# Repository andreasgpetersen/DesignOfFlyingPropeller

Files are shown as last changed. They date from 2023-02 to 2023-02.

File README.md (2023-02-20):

# Design Of Flying Propeller
Bachelor thesis at DTU 2020. This thesis focuses on building, programming, and controlling a novel type of dronedesign. The drone behaves like a helicopter rotor as it rotates around its z-axis to cre-ate the lift necessary to keep it airborne.

Test flight while suspended mid air: https://www.youtube.com/watch?v=Mw67W8S0a4E

The drone has three large wings, and rotates around its own z-axis to create lift, with one Teensy Microcontroller to control each wing. 
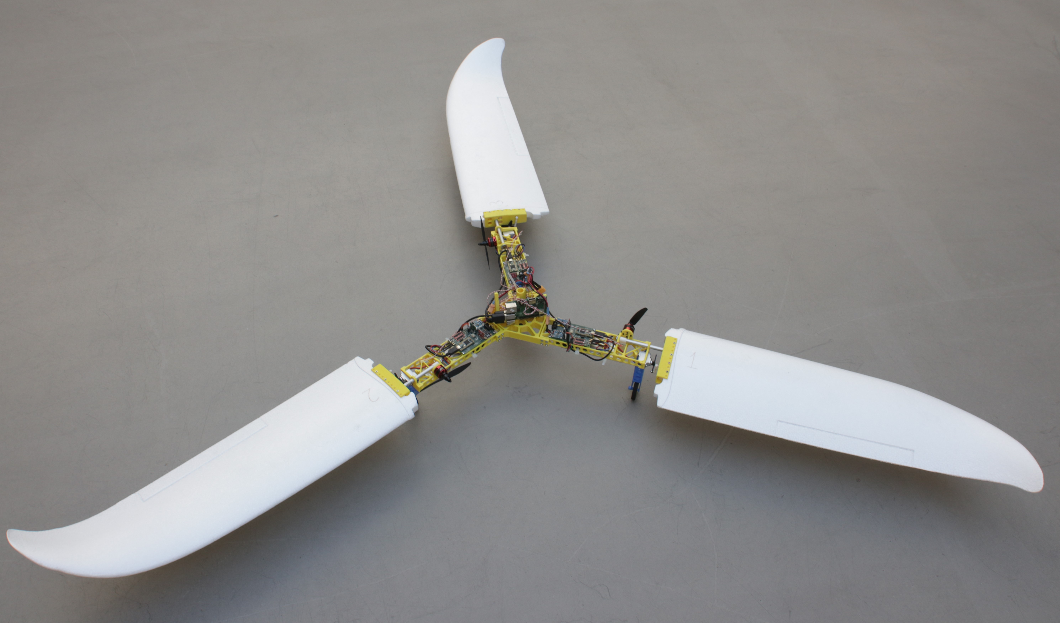
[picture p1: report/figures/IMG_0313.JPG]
Photo of final drone


All three Teensy boards send oirentation/location data to the Raspberry Pi which then computes the next control inputs. This runs in an infinite loop. The communication and power channels of the drones can be seen below: 
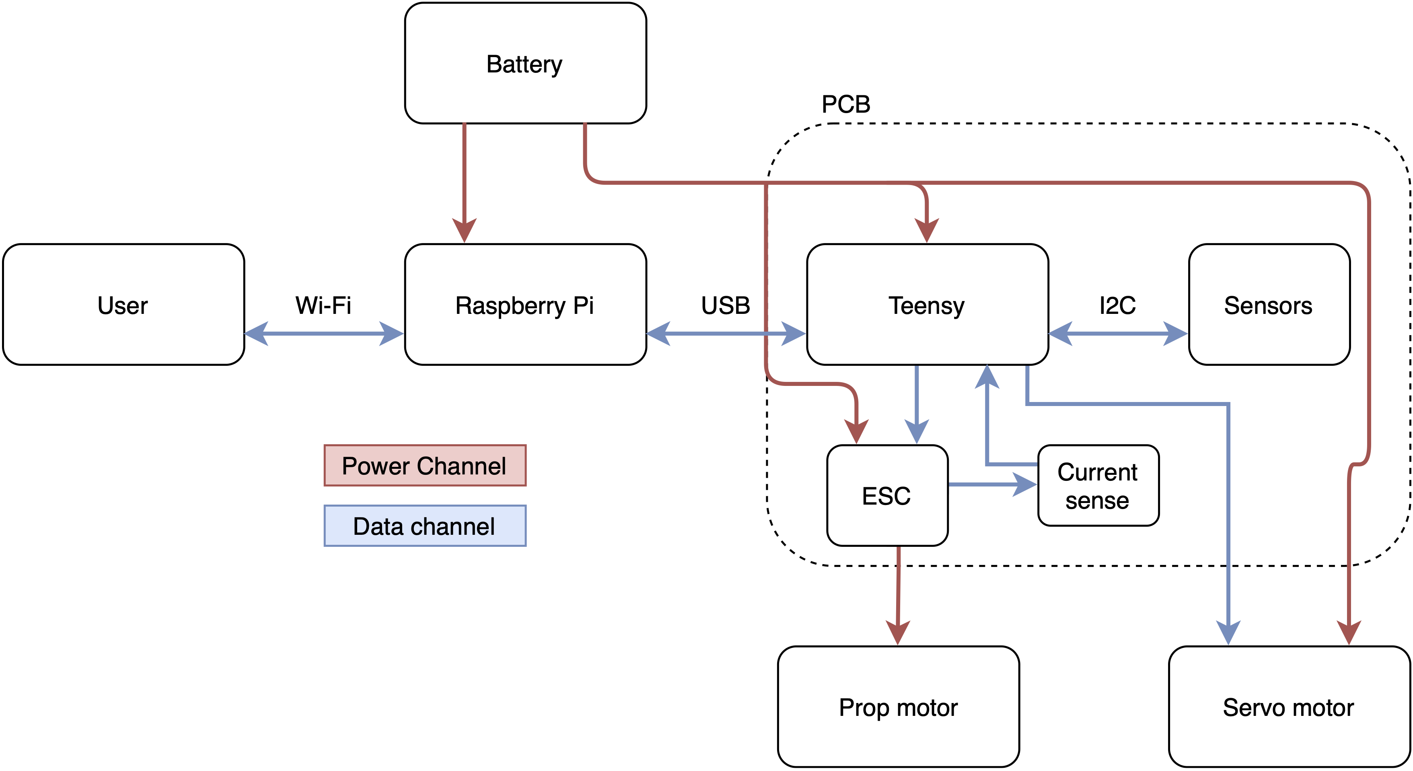
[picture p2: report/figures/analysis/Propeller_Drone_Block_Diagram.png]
Overview of communication and power channels


This code consists of two components:

1) communication_rpi2teensy, which is Python 3 code to be run on a Raspberry Pi (only tested for 3B+).
   The three Teensy board should be connected to the RPi using USB.
   In the folder you will find:

    A) communication_functions.py
    B) concurrent_control.py

	A) is a file that contains functions for communications for B) to execute
	B) is the main script which should be executed. Either it is configured for running a control loop
	with a set reference point, or it can be used as a menu for debugging functions. At all times
	the script logs data to a file which name is the days date and time. 
	
2) wing_ctrl_v2, which is C++ code that runs on a Teensy microcontroller (only tested for Teensy 3.2)
   In the folder you will find:
    A few example output log files
    B) .pio, which stems from PlatformIO. PlatformIO is used when programming the microcontrollers. It runs in 
    many IDEs and hackable text editors: https://docs.platformio.org/en/latest/integration/ide/vscode.html#installation
    C) .vscode which stems from Visual Studio code
    D) include, which is empty
    E) lib, which is empty but holds place for libraries
    F) src, which contains the code that runs on the microcontrollers
    G) test, which is empty
    H) platformio.ini which is used by PlatformIO extension
    
    F) is the only file that really matters, the rest is a byproduct of using PlatformIO. It runs a continous loop
    on the Teensy, in which it calculates orientation of the device and its sensor as well as issues commands
    to the propeller and servo motor

To use the code:
On the RPI, you download the scripts to a place of your choice, and run the scripts from the commandline
like you would with regular Python scripts, ie.: python3 concurrent_control.py 
Remember to install the approiate Python packages. The newest version of Python available on the RPi was used.
Consider using a virtual env to minimize errors with packages and versions. 

On the microcontroller, we used PlatformIO for programming. It runs well in Visual Studio Code.
To get started with PlatformIO follow the instructions here: https://docs.platformio.org/en/latest/integration/ide/vscode.html#installation
Remember to install Arduino IDE and Teensyduino: https://www.pjrc.com/teensy/td_download.html

When done, import wing_ctrl_v2 to PlatformIO and build the program. If you have trouble with libraries not being
found, remember to only build the code when you're in the wing_ctrl_v2 folder.
If it succeeds (which it does at the time of writing, June 25th 2020), upload it to each Teensyboard using
the inbuilt function in PlatformIO. Remember to change the boardnumber to the correct one to use the correct
calibration.

All boards are calibrated to be used in ASTA at DTU. If used elsewhere, recalibrate. 

This code has been developed by Jonas Brøndum (s173952@student.dtu.dk) and
Andreas Grønbech Petersen (andreasgp@protonmail.com / s173901@student.dtu.dk)
as part of a Bachelor Thesis in Electrical Engineering at DTU, June 2020

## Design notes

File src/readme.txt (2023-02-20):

Source code for Flying Propeller - A Bachelor Thesis 
This code consists of two components:

1) communication_rpi2teensy, which is Python 3 code to be run on a Raspberry Pi (only tested for 3B+).
    The three Teensy board should be connected to the RPi using USB.
    In the folder you will find:

    A) communication_functions.py
    B) concurrent_control.py

	A) is a file that contains functions for communications for B) to execute
	B) is the main script which should be executed. Either it is configured for running a control loop
	with a set reference point, or it can be used as a menu for debugging functions. At all times
	the script logs data to a file which name is the days date and time. 
	
2) wing_ctrl_v2, which is C++ code that runs on a Teensy microcontroller (only tested for Teensy 3.2)
    In the folder you will find:
    A few example output log files
    A) .pio, which stems from PlatformIO. PlatformIO is used when programming the microcontrollers. It runs in 
    many IDEs and hackable text editors: https://docs.platformio.org/en/latest/integration/ide/vscode.html#installation
    B) .vscode which stems from Visual Studio code
    C) include, which is empty
    D) lib, which is empty but holds place for libraries
    E) src, which contains the code that runs on the microcontrollers
    F) test, which is empty
    G) platformio.ini which is used by PlatformIO extension
    
    E) is the only file that really matters, the rest is a byproduct of using PlatformIO. It runs a continous loop
    on the Teensy, in which it calculates orientation of the device and its sensor as well as issues commands
    to the propeller and servo motor

To use the code:
On the RPI, you download the scripts to a place of your choice, and run the scripts from the commandline
like you would with regular Python scripts, ie.: python3 concurrent_control.py 
Remember to install the approiate Python packages. The newest version of Python available on the RPi was used.
Consider using a virtual env to minimize errors with packages and versions. 

On the microcontroller, we used PlatformIO for programming. It runs well in Visual Studio Code.
To get started with PlatformIO follow the instructions here: https://docs.platformio.org/en/latest/integration/ide/vscode.html#installation
Remember to install Arduino IDE and Teensyduino: https://www.pjrc.com/teensy/td_download.html

When done, import wing_ctrl_v2 to PlatformIO and build the program. If you have trouble with libraries not being
found, remember to only build the code when you're in the wing_ctrl_v2 folder.
If it succeeds (which it does at the time of writing, June 25th 2020), upload it to each Teensyboard using
the inbuilt function in PlatformIO. Remember to change the boardnumber to the correct one to use the correct
calibration.

All boards are calibrated to be used in ASTA at DTU. If used elsewhere, recalibrate. 

This code has been developed by Jonas Brøndum (s173952@student.dtu.dk) and
Andreas Grønbech Petersen (s173901@student.dtu.dk)
as part of a Bachelor Thesis in Electrical Engineering at DTU, June 2020

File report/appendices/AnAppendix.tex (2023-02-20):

%!TEX root = ../Thesis.tex
\chapter{Extra system graphics}
\begin{figure}[h]
    \centering
    
    \caption{Closed loop frequency response (from $\omega_{ref}$ to $\omega_{out}$) of controlled system}
    \label{fig:systemcontrollerbode}
\end{figure}

\begin{figure}[h]
    \centering
    
    \caption{Closed loop frequency response (from $\omega_{ref}$ to $\omega_{out}$) of controlled system with pitched wings}
    \label{fig:systempitchcontrollerbode}
\end{figure}

\begin{sidewaysfigure}
    \centering
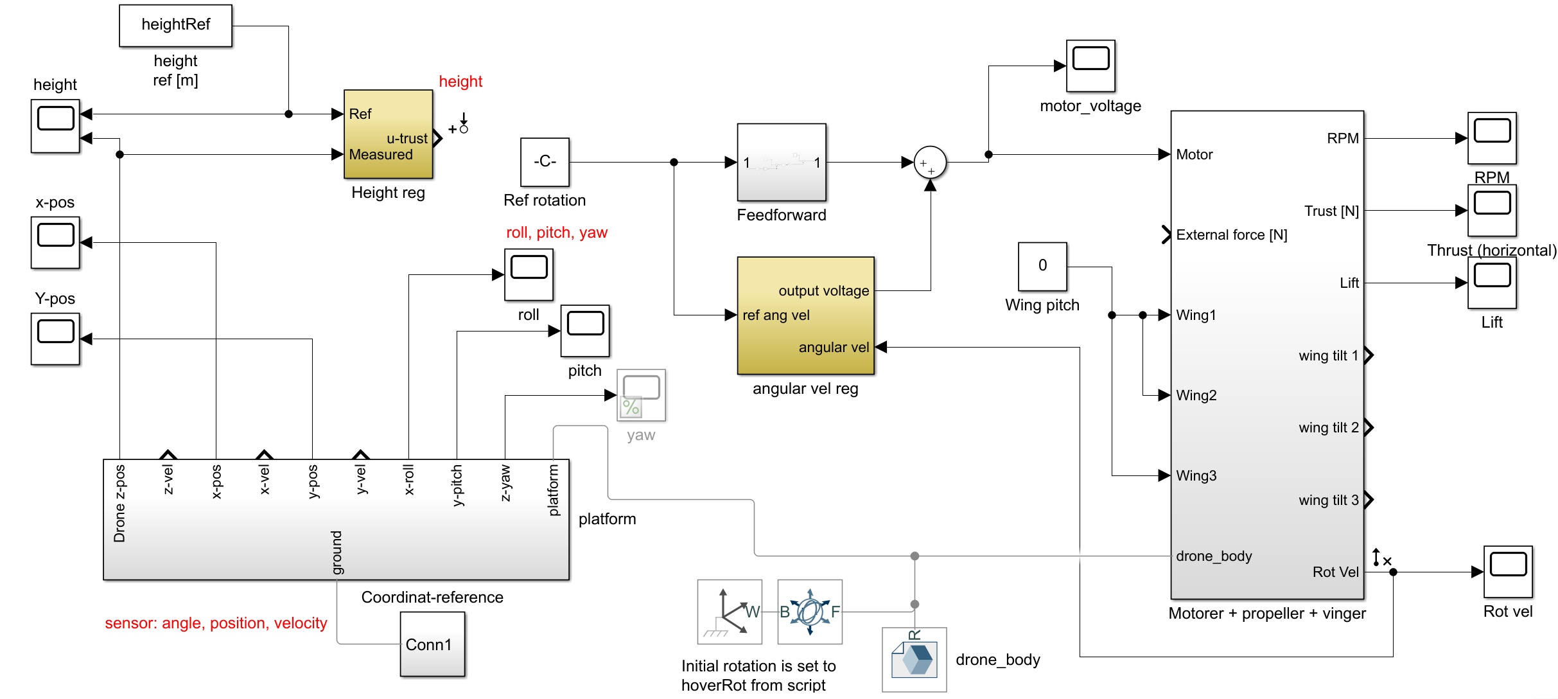
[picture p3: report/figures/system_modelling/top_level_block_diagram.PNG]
    
    \caption{Top level view of the Simulink model of the drone}
    \label{fig:toplevelmodel}
\end{sidewaysfigure}

\chapter{Video of flight test}
\href{https://youtu.be/Mw67W8S0a4E}{Link} to drone flight test: https://youtu.be/Mw67W8S0a4E\label{link:droneflight}

\chapter{Yaw drift test}
\begin{figure}[h]
    \centering
    
    \caption{Test of yaw drift. Measured for approximately 6 minutes. Manually did a rotation of about 170 degrees after 4 minutes}
    \label{fig:yawdrifttest}
\end{figure}

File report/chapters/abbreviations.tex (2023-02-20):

\textbf{List of abbreviations and phrases}
\begin{itemize}
    \item RPM = Revolutions pr minute
    \item ESC = Electronic speed controller
    \item PWM = Pulse width modulation
    \item RPi = Raspberry Pi 
    \item AoA = Angle of attack
    \item IMU = Inertial measurement unit
    \item PCB = Printed circuit board
    \item ROM = Read-only memory
    \item EOL = End of line
    \item OS = Operating System
    \item DPS = Degrees per second
    \item mutex = mutual exclusion
    \item ISR = Interrupt service routine
    \item SysID = System Identificiation Toolbox
    \item SISO = Single input single output
    \item Li-PO = Lithium-ion polymer battery
    \item SSH = Secure Shell
    \item Servo motor = A type of precise and strong motor. Used in this project only to control the wing tilt angle. Sometimes referred to as "wing tilt motor" or "wing pitch motor".
    \item Propmotor = propeller motor
\end{itemize}

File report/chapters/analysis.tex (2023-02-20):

\chapter{Problem analysis}
\section{State of the art} \label{sec:stateoftheart}
Stationary hover of drones is a subject with many known solutions, including quadcopters. Traditional quadcopters and other multirotor drones of similar design can obtain very high speeds, but consequently are quite ineffective with considerable power draws. Ineffective, meaning short flight times relative to the weight of the drone and its battery capacity. Drones from industry leaders such as DJI or Autel Drones typically have a flight time of approximately 30 minutes \cite{mavic2} \cite{MG-1} \cite{AutelEvo}.
The endgame for the proposed drone-design is an aircraft that can stay in the same location for long periods of time. With an efficient design, it should have low power usage with a small weight and great lift, resulting in much longer flight duration than traditional multirotor drone designs. 

\section{Previous work}
The drone used in this project is not an off-the-shelf product. Associate Professor Jens Christian Andersen made all the preliminary work and design choices.\\
The drone can be seen below in fig. \ref{fig:topviewdrone} and \ref{fig:bottomviewdrone}. A close-up of an arm can be seen in fig. \ref{fig:dronearmcloseup}.\\
At the beginning of the project period, the drone was equipped with some motors, custom PCB with sensors, microcontrollers, and a Raspberry Pi (RPi). A substantial amount of code had been written, especially for the microcontrollers and some for the Raspberry Pi, though the drone did not function at the time. 
The drone body is made from 3D printed plastic. As much as possible of this work will be reused.\\
\begin{figure}[h!]
    \centering
    \begin{minipage}[t]{.48\textwidth}
        \centering
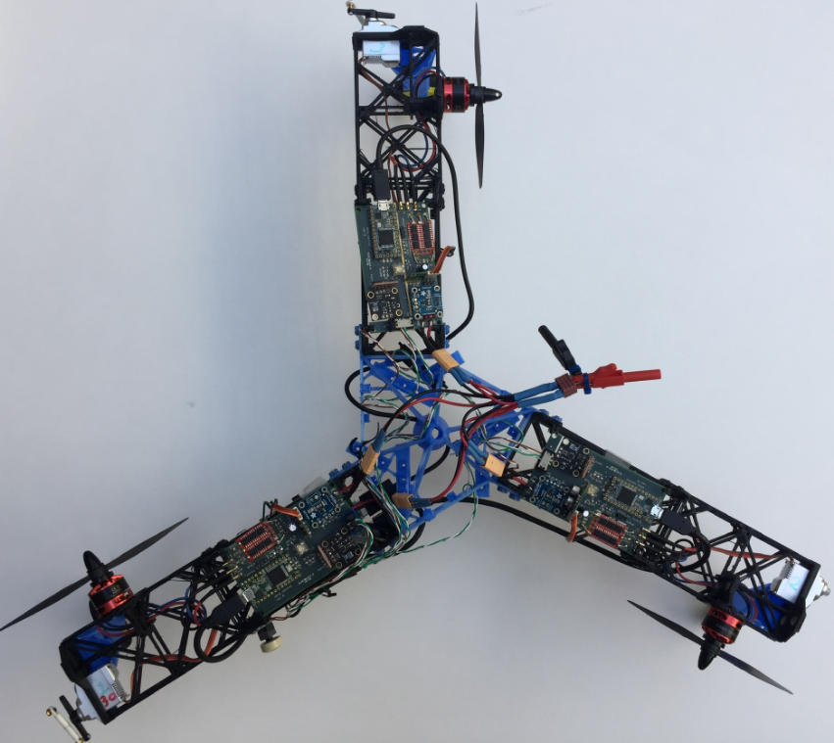
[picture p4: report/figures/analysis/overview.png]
        
        \caption{Overview of the drone. Notice each arm has one propeller motor, one wing tilt servo motor and one module with sensors etc}
        \label{fig:topviewdrone}
    \end{minipage}%
    \hspace{.03\textwidth}
    \begin{minipage}[t]{0.48\textwidth}
        \centering
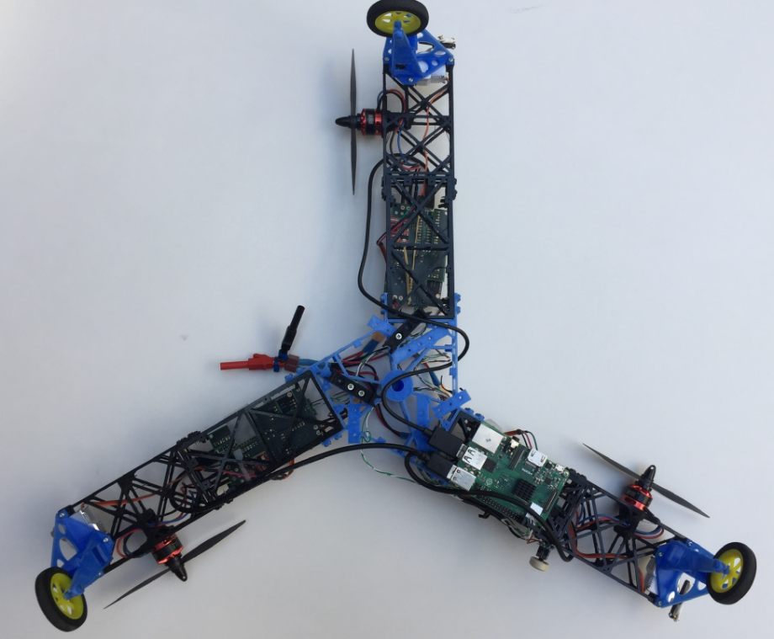
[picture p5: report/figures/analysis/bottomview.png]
        
        \caption{Bottom view of the drone. Notice the Raspberry Pi, and lack of batteries}
        \label{fig:bottomviewdrone}
    \end{minipage}
\end{figure} 

\begin{figure}[h!]
    \centering
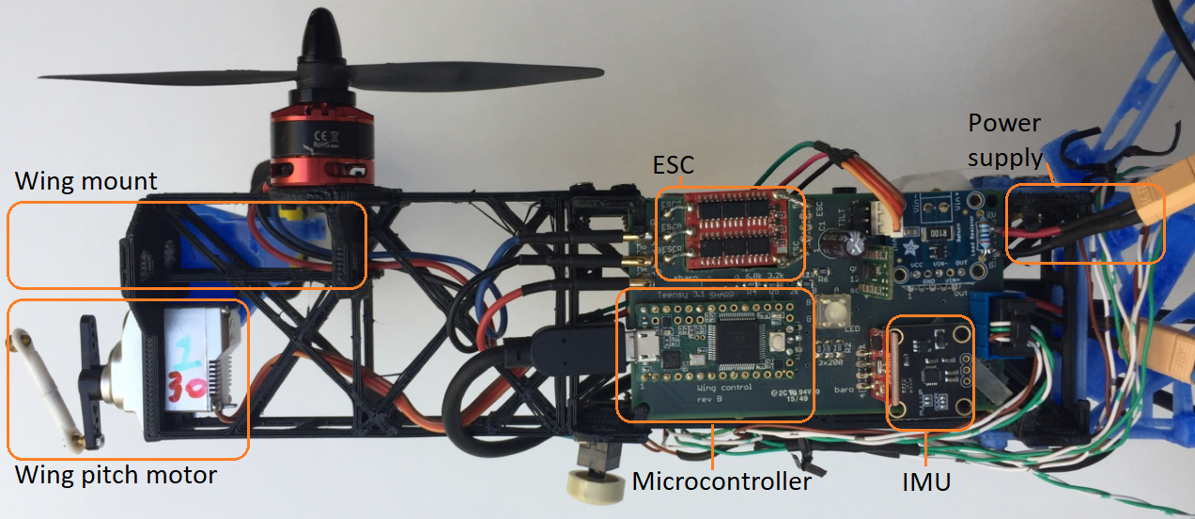
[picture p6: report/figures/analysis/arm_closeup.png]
    
    \caption{Close up view of one drone arm}
    \label{fig:dronearmcloseup}
\end{figure}
The following subsections elaborate upon the details of the drone.

\subsection{Motors}
There are two types of motors on the drone: the propeller motor, which creates forward thrust to spin the drone in a circular motion, and the wing tilt motor that controls the tilt of the wing. \\
The propeller motor is a 2300 kV brushless DC motor for 3S and 4S battery configurations \cite{propellermotordata}, which means that the motor needs a battery with 3 or 4 cells in series to have sufficient voltage to run. The kV rating suggests it will approximately run 2300 RPM per volt across the motor with no load.  \\
The wing tilt motor is a 3 Blue Bird BMS 380 Max servo motor, and can be configured from 4.8V to 6V \cite{tiltmotor}. Continuous PWM-signals control it. The motor is quite capable -- at 6V it has a torque of 4.7 $kg\cdot cm$. 

\subsection{Modules} 
Each of the drone's three arms consists of a printed circuit board (PCB) with multiple sensors, a few small circuits, and a microcontroller. 
The components are:
\begin{itemize}
    \item A Teensy microcontroller version 3.2 \cite{teensy32}.
    \item An MPU-9250; a 9-DoF inertial measurement unit (IMU) with accelerometer, gyroscope, and magnetometer. \cite{mpu-9250}.
    \item A BMP180 barometric pressure, temperature, and altitude sensor \cite{BMP180}.
    \item An INA169 analog current sensor breakout board using the INA169 current shunt monitor from Burr-Brown \cite{INA169}.
    \item A 10A UBEC electronic speed control that uses Li-Po batteries \cite{HK10AESC}.
    \item An RGB LED
    \item A D24V22F6, which is a 6V, 2.5A Step-Down Voltage Regulator from Pololu \cite{PololuStepDown}.
    \item Supporting circuitry, input- and output pins for power and data transmission.
\end{itemize}
The converter steps down the voltage from the batteries to 6V usable by the wing tilt motor. The ESC controls the propeller motor. Barometer, MPU-9250, and INA169 are used to obtain data about the drone and its state. The microcontroller ties everything together.
%and facilitates the communication between arm and Raspberry Pi. 

\subsection{Microcontroller}
A Teensy 3.2 microcontroller is used to monitor and control all that happens on each arm. The Teensy's goal is to receive sensor data and communicate with the CPU. The microcontroller also streamlines the received data into easy-to-read formats (SI-units) for both the CPU and user.

\subsection{CPU} %
The drone's CPU is a Raspberry Pi (RPi) 3B+. It is responsible for centralizing data from all three arms and the processing of it. The processed data establish the changes to the propeller motor's RPM and the servo motor's position for each arm. As such, the RPi transmits commands that invoke the necessary changes. 

\section{Analysis of objectives}\label{analysisofgoals}
For the drone to control its rotational speed relative to a reference point, some hardware work must be done. It is necessary to have a fully functioning hardware setup before any other work can start. Due to the nature of this project, much work must go into this, as it is a physical prototype of this new design. \\
Reliable communication between microcontrollers and the RPi is crucial because otherwise, no data transfer or calculation can be made. When this is complete, the sensor usage can begin, and it should then be possible to start analyzing the data in real-time to gain information about the orientation and state of the drone.  \\
In the end, a control loop can be implemented either in a simulation using a model or on the prototype, with the goal of stabilizing the rotational speed in reference to a set point. \\
An in-depth analysis of what specifically needs to be done can be seen in the next five subsections.

\subsection{Hardware design}\label{hardwaregoals}
Three main goals have to be completed:
\begin{enumerate}
    \item Constructing a suitable battery pack that has the correct specifications and an appropriate capacity. The capacity has to be high enough to endure long flight times, but also not too heavy for efficient flight. 
    \item Programming the microcontroller so that all sensors are usable, and both the propeller and wing tilt motor can be controlled. Functions for sending and receiving data are needed as well.
    \item Choosing wings of an appropriate design and mounting them. Wing types and designs have to be analyzed, and an appropriate way to fit them is needed. They have to be mounted both on the drone body, and to the wing tilt motor so the pitch can be controlled. 
\end{enumerate}
These goals will be explored in chapter \ref{chap:comm_hardware}. 

\subsection{Communication}\label{commgoals}
The primary objective is to design easy to use and "fast enough" communication between the microcontrollers and RPi, relative to the needed update frequency of the control loop. A concurrent programming solution will be considered.
This goal will be explored in chapter \ref{chap:comm_hardware}.

\subsection{Sensor data and usage}\label{sensorgoals}
For sensor data, two main objectives have to be achieved:
\begin{enumerate}
    \item Stable outputs of sensors that result in good measurements and usable data. 
    \item Combining sensor data to gain knowledge about roll, pitch, and yaw, as well as where the drone is in its rotation and its orientation relative to true north. 
\end{enumerate}
These goals will be explored in chapter \ref{chap:sensordataandusage}.

\subsection{Control loop}\label{controlloopgoals}
A well-functioning control loop has to be implemented. A good loop will hopefully result in fast, and stable performance, that lets the drone react to small irregularities as well as significant changes. This loop will have one key objective: to control the rotational velocity of the drone. A PD-controller with a feed-forward branch will be examined in chapter \ref{controlloopchapter}.

\subsection{System modelling}\label{modelgoals}
The system will be simplified and modeled using Matlab and Simulink for gathering and analyzing comparable data. Additionally, the model will be used for preliminary testing of the drone's capabilities and its controller.
This goal will be explored further in chapter \ref{chap:systemmodelling}, and implemented in section \ref{results:rotcontroller}.

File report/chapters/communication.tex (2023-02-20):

\chapter{Hardware and communication design}
\label{chap:comm_hardware}
%%Start af chapter:
As mentioned previously, a large portion of the project has been devoted to restructuring, and the further development of both hardware and software. Some aspects have been re-purposed to fit the previous knowledge and experience of the project managers. The goal of this chapter is to describe what physical changes have been made to the drone. It also aims to describe the general communication routine.

\section{Physical restructuring}
For finalizing the drone's basic functionality, a battery pack and wings were added to the drone. When addressing the drone, \texttt{arm 1}, \texttt{arm 2} and \texttt{arm 3} is used to denote whichever arm is in question. This applies to all chapters. 
\subsection{Wings}
The drone is retrofitted with three right-hand side wings (with respect to a normal RC plane). The wings have a length of 64 cm and a width of 20 cm at the root, which tapers into the wingtip. The chord line is the same length as the width at 20 cm (see fig. \ref{fig:wing}). The wings' camber (amount of asymmetry in relation to the chord line) was approximated to around 4\% \cite{camber, lift_coefficient}. Additionally, the wings have small winglets. Analysis of the wing's drag and lift is carried out in section \ref{chap:wing_est}. \\
Initially, other wings were chosen and ordered for the drone, but given that they were late in shipment, these wings were used instead. This resulted in use of wings with less lift, as these were smaller than the ones that were ordered. 

\begin{figure}[h!]
    \centering
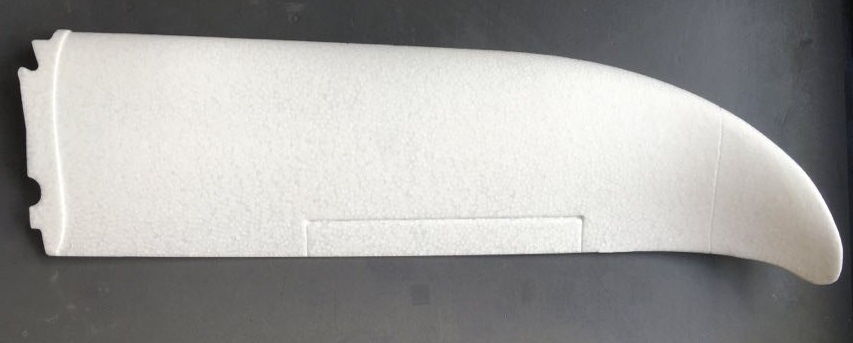
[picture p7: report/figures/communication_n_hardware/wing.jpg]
    
    \caption{The wing type attached to each arm of the drone}
    \label{fig:wing}
\end{figure}
The wings are glued to aluminium rods and screwed into 3D printed brackets. These 3D printed brackets are attached to the servo motors of each arm, such that a rotation of the horn of the servo motor, leads to a rotation of the wing.

\subsection{Battery pack}
The battery pack consists of 3 separate Li-PO cells. Each cell has a 5000 mAh capacity at a voltage of $V_{cell} = 3.7$ V. Each cell has a discharge rate of 20C. The total weight of the battery pack containing three cells is $0.342 \,kg$. The capacity-to-weight ratio of this battery pack was deemed to be a good starting point for the drone. The cells were soldered together and placed on the bottom side of each arm to avoid interfering with the drone's center of mass \cite{battery}. The cells were wired in a series connection to reach the desired voltage of roughly 11 V.

\subsection{Additional adjustments}
In the drone's original design, each PCB was attached to the drone's frame by four elastic bands, one in each corner of the PCBs. This was done to avoid unwanted measurement errors from shaking and rattling. This design was deemed impractical, so three new modules were printed to attach the PCBs with screws to keep them static with respect to the drone's frame.\\
Moreover, each PCB was retrofitted with new voltage step-down regulators that can supply the servo motors with more power. Likewise, a faulty IMU was replaced.

\section{Data channels}
The drone's interconnected components do not require any significant communication speeds. Therefore, the I2C-protocol was deemed impractical, and further development on communication between the RPi and the Teensy via I2C was discontinued. Instead, a more convenient option of USB communication was decided upon.\\
An overview of the drone's data and power channels can be seen in fig. \ref{fig:blockdiagram}.
\begin{figure}[h!]
    \centering
    
    \caption{The drone's power and data channels}
    \label{fig:blockdiagram}
\end{figure}
The previous methods for USB communication between the microcontroller and the RPi have remained. Earlier, this was only for debugging purposes, but ultimately preferred due to ease of use. The RPi sends a command, that the Teensy can interpret. The microcontroller replies via USB with the requested information. The user connects to the RPi using SSH.\\

Data between the microcontroller and the sensors was transmitted and received through the I2C-protocol. This was set up before the beginning of the project. Subsequently, this communication method has been tweaked to supply the system with reliable sensor measurements.\\ 
An interrupt pin on the IMU has been connected to the Teensy. The interrupt pin serves to signal that new data is available from the sensor. This ensures that the microcontroller receives data when available and does not need to request new data. 

\subsection{Drone routine}
The RPi and the microcontrollers are connected by USB. Information is only exchanged between the two devices when the RPi asks for it. The RPi sends a string with a distinct format specifying a command. There are two types of commands: ones that make the microcontroller return data and those that adjust values for the motors, i.e., setting a new angle for the wing tilt. The RPi is programmed in Python 3, and the microcontrollers are programmed in C++. All source code is attached to the hand-in on DTU Inside.

On the microcontroller, a buffer is filled with data from the USB connection. If the last character is an EOL sequence, a routine that reads and reacts to the information in the buffer, is invoked. For a Linux based OS, the EOL sequence typically is "\textbackslash n". 
The RPi utilizes a similar routine, also looking for a byte stream ending with an EOL sequence. The byte stream is converted to ASCII characters, and then the RPi reacts upon the data. 

For this application, the RPi has to communicate with three microcontrollers. A concurrent solution was implemented to minimize downtime when transferring data between devices. The concurrent solution was deemed superior to a sequential or parallel solution, due to the amount of IO tasks and downtime associated with waiting for data. A comparison of concurrent and parallel solutions can be seen in table \ref{tab:conccurentvsparallel}. Even though a parallel solution could potentially be faster, the before-mentioned wait time and lack of heavy computations would likely result in the same performance between the two solutions. Furthermore, the concurrent one is far easier to implement. 
\begin{table}[h]
\centering
\resizebox{\textwidth}{!}{%
\begin{tabular}{|l|l|l|}
\hline
 &
  Pros &
  Cons \\ \hline
Concurrent &
  \begin{tabular}[c]{@{}l@{}}- Ease of use\\ - Implementable on single-core systems\\ - Good for reducing down-time \\ when doing multiple IO tasks at once\end{tabular} &
  \begin{tabular}[c]{@{}l@{}}- Slower for some types of tasks\\ - Not true parallel functionality\end{tabular} \\ \hline
Parallel &
  \begin{tabular}[c]{@{}l@{}}- Generally faster when setup is done \\
  -Effective for computationally difficult\\ tasks (great for matrix multiplication,\\ 3d rendering etc.)\end{tabular} &
  \begin{tabular}[c]{@{}l@{}}- Higher complexity\\ - Need multi-core hardware\\ - Higher base resource usage\end{tabular} \\ \hline
\end{tabular}%
}
\caption{A comparison of concurrent and parallel programming}
\label{tab:conccurentvsparallel}
\end{table}

Each time the RPi needs data, it runs a function that spawns three threads. The function call takes a serial object as argument. This object defines which of the microcontrollers a given thread connects to.
The threads then communicate with the microcontrollers, and, if applicable, write data to arrays on the RPi. When finished, the threads shut down. Hereafter, new threads can be spawned with a new function call. This results in a stable sampling rate between the RPi and the microcontrollers of $f_s \approx 30 Hz$.

Typically, there can be mutual exclusion (mutex) / race condition issues when having multiple threads edit the same data, but in this application, they only edit one cell in an array with an index associated explicitly with that thread. One thread then sorts the data into the correct places. Only one thread takes care of writing data to log files. Thus, mutex issues are not a problem. 

The routine that runs on the RPi, which utilizes concurrency can be seen in fig. \ref{fig:droneroutinechart}. All communication is done using multiple threads.

\begin{figure}[h]
    \centering
    
    \caption{A flowchart of the routine running on the RPi. After starting the script, then the board numbers are read from the microcontrollers to ensure correct indexing when writing commands to each arm. Afterwards, an infinite loop runs. User input and logging of data can be used as needed}
    \label{fig:droneroutinechart}
\end{figure}
The control loops in the routine will be examined in detail in chapter \ref{controlloopchapter}. 

Before the microcontrollers are ready to receive commands from the RPi, they perform a setup routine. Here, the microcontroller initializes all the needed IO pins, I2C and serial busses, ESC, and the IMU. The IMU performs a brief calibration of the gyroscope and accelerometer. This setup is only done once when the microcontroller boots. When this routine is done, it enters an infinite loop. 

In this loop, it receives data from the sensors, runs a filter fusion algorithm (see chapter \ref{chap:sensordataandusage}), plus checks the USB buffer and reacts upon its content, i.e., writing new PWM values to the propeller motors.
As mentioned previously, the MPU9250 is configured with an interrupt-based connection. 
This means that it sends an interrupt signal to the microcontroller, which then invokes an ISR. This routine makes the microcontroller read from the I2C connection. The interrupt signal is only sent when all registers on the MPU9250 have been filled with data. After each interrupt, the MPU9250 clears all data register and reads new data from its sensors.  

\section{Chapter summary}
The general physical construction of the drone was finished with wings, battery pack and additional components. The RPi and microcontrollers were fitted with software so they could communicate, send signals to the motors and read data from sensors. The objectives outlined in section \ref{hardwaregoals} and \ref{commgoals} have been fulfilled. Lift and drag coefficients for the wings will be estimated experimentally in section \ref{chap:wing_est}. The speed of communication between microcontrollers and RPi are commented upon in section \ref{error_measurementprecision}. All source code is attached to the hand-in on DTU Inside.

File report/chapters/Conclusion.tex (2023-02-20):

%!TEX root = ../Thesis.tex
\chapter{Conclusion}\label{chap:conclusion}

This thesis presents a solution to the drone's rotational controller as well as orientation estimation based on sensor measurements. A novel drone design similar to the one of a helicopter, was explored.\\
The orientation estimation was implemented with a filter fusion algorithm using the IMU's sensor data. An estimation was able to locate the drone in its rotational position regarding the true north. These tests were carried out both on and off the ground. The estimation performed reliably at small velocities but fared worse at larger velocities. \\

The drone was fitted with wings, and a new frame, such that it could sustain the forces applied when in motion.
The drone's natural transfer function from motor voltage to rotational velocity was derived and used to develop a controller.\\
The controller designed was able to respond fast to changes in reference point due to its feed-forward branch. It was shown that the drone needed a PD-controller, which resulted in exceptional fine-tuning, but also the system damping required to minimize any overshoot. 
Finally, the drone was able to take off when tested for lifting capabilities. It was shown that the drone could take off under the right conditions.\\
In conclusion, the objectives listed in section 1.2 are fulfilled, and the drone functions as intended.

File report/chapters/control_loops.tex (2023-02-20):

\chapter{Control loop}\label{controlloopchapter}
In this chapter the simplified physics and SISO linear control theory will be presented. First, the physical link between hover and rotation is developed in section \ref{sec:preliminaryphysics}. Afterwards, constraints of the drone are examined. Finally, how to derive a transfer function for the system, and control it, will be reviewed. Table \ref{tab:constants} shows relevant constants that characterize the system and/or are used for calculations.

\begin{table}[h!]
\centering
\renewcommand{\arraystretch}{1.3}
\begin{tabular}{|l|l|l|}
\hline
Description                & Notation    & Value \\ \hline
Gravitational acceleration & g           & $9.81 \,\frac{\text{m}}{\text{s}^2}$                              \\ \hline
Mass of drone              & $m_{drone}$ & $1.41 \,\text{kg}$  \\ \hline
Air density                & $\rho$      & $1.225 \,\frac{\text{kg}}{\text{m}^3}$                             \\ \hline
Length of arm              & $l_{arm}$   & $0.27\,\text{m}$                              \\ \hline
Length of wing             & $l_{wing}$  & $0.64\,\text{m}$                              \\ \hline
Area of wing               & $A_{wing}$  & $0.121\,\text{m}^2$ (fig. \ref{fig:wing_area_approx})                             \\ \hline
Motor velocity constant    & $K_v$       & $2300$\, $\frac{\text{RPM}}{\text{V}}$       \\ \hline
Motor torque constant      & $K_T$       & $0.0042\, \frac{\text{N}\cdot\text{m}}{\text{A}}$                            \\ \hline
\end{tabular}
\caption{Table of relevant constants}
\label{tab:constants}
\end{table}

\section{Preliminary physics}\label{sec:preliminaryphysics}
For hover conditions, the forces acting on the drone sum to zero. The physical forces acting on each arm are illustrated in fig. \ref{fig:kraftdiagram}.
\begin{figure}[h!]
    \centering
    
    \caption{Diagram of the forces acting on each wing in a hover state}
    \label{fig:kraftdiagram}
\end{figure}
The gravitational forces and lift are calculated for the entire drone (eq. \ref{eq:gravity}), while the horizontal forces of thrust and drag are characterized as internal forces acting on each wing and arm of the drone.  
\begin{equation}
\label{eq:gravity}
    F_t = \frac{1}{3}\cdot m_{drone} \cdot g 
\end{equation}
For hover conditions, the lift must be equal to the gravity acting on the drone, necessitated by Newton's second law of motion. \\
The lift, or upwards thrust, is characterized as (\cite{flight_physics}) the lift induced by a conventional tapered airfoil (eq. \ref{eq:lift}). Eq. \ref{eq:rot2speed} is used when converting from angular velocity to velocity.
\begin{align}
    \label{eq:lift}
    L &= \frac{1}{2}*\rho*v^2*A_{wing}*c_L\\
    v &= \omega * r \label{eq:rot2speed}
\end{align}
$\rho$ is the density of the air.
$A_{wing}$ is the surface area of the wing, which has been approximated as shown in fig. \ref{fig:wing_area_approx}.
\begin{figure}[h!]
    \centering
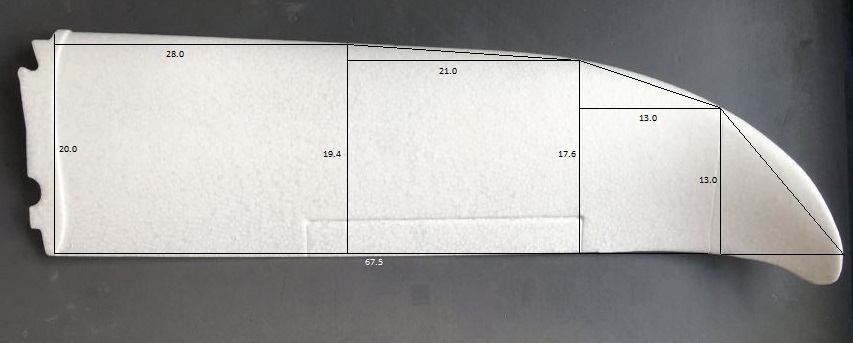
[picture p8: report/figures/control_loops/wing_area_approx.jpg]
    
    \caption{Approximation of wing surface area}
    \label{fig:wing_area_approx}
\end{figure}\\ 
Since the wings are rotating around the center, the wings' speed will be proportionately larger further away from the center. The wings' velocity can be modelled as a function of their rotational velocity, $\omega$ (eq. \ref{eq:rotvel}). 
The average rotational velocity is calculated from "copying" the wing into N wings, each with a velocity corresponding to the inner radius plus its iterational value (ie \textit{i}), or number (eq. \ref{eq:omega_approx}). This is done with a simple for-loop that sums all rotational velocities, $\omega$, and divides with the number of wings, N. For increasingly larger N, this number converges to a slightly better approximation than that of a regular mean over the wing's length. $N=10^6$ was found to be an appropriate size. 
\begin{align}\label{eq:rotvel}
    \omega_i &= \frac{\sqrt{\frac{\frac{2}{3}*m_{drone}*g}{\rho*c_L*A_{wing}}}}{r_{inner}+\frac{i*L_{wing}}{N}}\\
    \omega_{avg} &= \frac{\sum_{i=0}^{N} \omega_i}{N+1}
    \label{eq:omega_approx}
\end{align}
The final variable, $c_L$, is set to a constant value for this calculation.
The lift coefficient, $c_L$, is dependent on the angle of attack (AoA) and can be experimentally calculated. The drag coefficient (denoted $c_D$) and lift coefficient, are calculated with NASA's Foil Sim applet for airfoil approximations. The wing's characteristics can be seen in fig. \ref{fig:liftcoefficient} \cite{lift_coefficient}.

The ratio between lift and drag is also calculated with the applet and can be seen in fig. \ref{fig:LDratio}.

\begin{figure}[h!]
    \centering
    \begin{minipage}[t]{0.48\textwidth}
        \centering
        
        \caption{The theoretical lift and drag coefficient as a function of the AoA}
        \label{fig:liftcoefficient}
    \end{minipage}%
    \hspace{.03\textwidth}
    \begin{minipage}[t]{0.48\textwidth}
        \centering
        
        \caption{The theoretical lift-to-drag ratio as a function of AoA}
        \label{fig:LDratio}
    \end{minipage}
\end{figure} 
Although the drone's horizontal axis will be spinning at a constant speed, it is increasingly difficult to calculate and approximate the thrust generated from a propeller motor. Therefore, calculating the motor voltage to lift ratio would require far too many approximations. As such, the results would carry no relevant information to the drone's practical characteristics and, therefore, has not been done. 
Henceforth, the angular velocity will be the measure of the physical model's accuracy.

Varying the lift coefficient, $c_L$, while using the method in eq. \ref{eq:omega_approx}, yields rotational velocities as shown in fig. \ref{fig:liftvariation}

\begin{figure}[h!]
    \centering
    
    \caption{The average rotational velocity required to hover as a function of the lift coefficient, $c_L$, ($N=10^6$)}
    \label{fig:liftvariation}
\end{figure}

\section{Constraints}
The drone has some physical constraints related to how it was constructed, as it is an atypical drone design. These constraints will have to be considered in the assembly of the control loop.
\begin{itemize}
\label{list:constraints}
    \item The motors are wired in such a way that they are only provided positive voltages. Consequently, they will only be able to spin clockwise (spinning the drone counter-clockwise), thereby creating thrust in their positive z-direction (one-way horizontal rotation).
    \item The wing pitch is very restricted in articulation, as seen in fig. \ref{fig:liftcoefficient}. Any AoA out of this range will most likely cause stalling.
\end{itemize}

\section{System controller}
In this section, design of the system controller will be examined. To be able to control the angular velocity, the drone's physical properties from motor voltage to rotation need to be determined. This means deriving the natural transfer function, which can be found from the step response of the system. 
The finished control system consists of one controller, that will regulate the drone's angular velocity around its z-axis based on a set reference point. \\
The controller will output voltages that adjust the propeller motors to maintain a steady velocity.

\subsection{Natural transfer function of the system}
In this section, it is discussed how a natural transfer function for the system can be derived. The drone will receive a step in voltage, when it's in a steady state rotation, where the output angular velocity will be analyzed both manually and correlated with the assistance of Matlab's Systems Identification Toolbox \cite{SysidToolbox}. This step will be conducted both on- and off-ground.\\

\textbf{Deriving a transfer function:}\\ \label{tf_teori}Manually deriving a transfer function from an open-loop step response can realistically only be done for a very simple system with one or two poles in the same location. For the 2nd order system with coinciding poles, the damping ratio is unity. This is also known as the over-dampened case. Here, the poles are real and negative.
To find this pole, the time constant, $\tau$, must be found. $\tau$ is located as the point in time when the output has reached 63.2\% of its final value. The pole is then found as the negative inverse of $\tau$ \cite{reguleringsbog}. For a 1st order system of the following form, $h(s) = \frac{b}{s+a}$, the static gain is found as $\frac{b}{a}$. From this expression, \textit{b} can be isolated. 

Otherwise, to determine a transfer function for a system, a tool like System Identification Toolbox is useful \cite{SysidToolbox}. It uses a nonlinear least-squares algorithm to fit a user-specified number of poles and zeros to the given data. The data is a step starting from 0, both with input values and output values. It returns a fitted transfer function and a percentage of how good the fit is. 

When analysing the results, a 1st order transfer function will be derived manually once. Thereafter, System Identification Toolbox will be used instead. 

\subsection{Controller type}
As previously mentioned, the drone has physical constraints, therefore the implemented controller will need to have an insignificant overshoot. A differential controller of the right proportions will ensure the right amount of damping and that the overshoot is minimal or non-existent. \\
To ensure minimal steady-state error along with system stability and a fast-enough response, a proportional gain is a natural addition to the differential part. However, the proportional gain is restricted to small values due to the physical constraints of the prop motors' input voltage range. \\
Furthermore, in the process of keeping the controller's response precise and relevant, a simple feed-forward element will be implemented to account for any significant discrepancies. The feed-forward branch works to complement the feedback PD-controller, as it maintains a rather fast overall response of the system. \\
The block diagram is in fig. \ref{fig:controlblock}.

\begin{figure}[h!]
    \centering
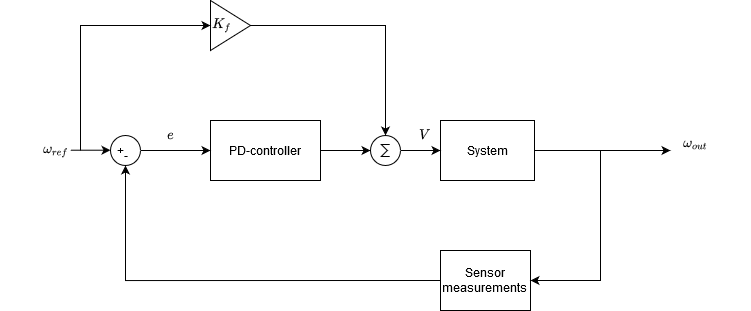
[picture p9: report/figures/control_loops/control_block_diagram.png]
    
    \caption{Block diagram of PD control loop with a feed-forward branch}
    \label{fig:controlblock}
\end{figure}

The values of $K_P$ and $K_D$ will be determined from the system transfer function. The feed-forward gain, $K_f$ will be found by approximating the linear relationship between motor voltage and angular velocity. From this, an expression will be derived. It will act as a system "predictor". \\
For the system, the feed-forward will act as a coarse adjuster, while the PD-controller will act as a fine-tuner.\\
The final closed-loop transfer function becomes (with system named $A(s)$):
\begin{equation}
    G(s) = \frac{\omega_{out}(s)}{\omega_{ref}(s)} = \frac{A(s)*\left(PD(s)+K_f\right)}{1+A(s)*PD(s)}
\end{equation}

\section{Chapter summary}
This chapter introduced the physics of the drone in a hover state. An approximation of the wings' properties was derived, and a controller to regulate the drone's angular velocity was proposed. Additionally its block diagram as well as transfer function were examined. Finally, ways of determining a transfer function from a step response was elaborated upon.\\
The groundwork for a well-functioning control loop has been made. Derivation and implementation of transfer functions and control loop, as well as performance evaluation will be completed in section \ref{results:rotcontroller}.

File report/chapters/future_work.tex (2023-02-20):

\chapter{Future Work}\label{chap:futurework}
Further improvements and future work consist of (but are not limited to):
\begin{itemize}
    \item Physical changes in both wheels and wing types
    \item Increasing RPi sample rate by improving communication
    \item Tilt controller, for a more stable flight
    \item Rotational based height regulator. This would require new height measuring devices e.g., sonic sensor et al.
    \item Software fail-safes to increase robustness and safety of the drone
    \item Exploring other purposes for this drone-type
\end{itemize}

\section{Physical changes}\label{sec:futureworkphysicalchanges}
The most significant drawbacks of the current state of the drone have proven to be the wings and the wheels.\\
As seen from the final flight tests, the drone does not have the necessary power to lift and maintain a hover condition for itself. This can be fixed either with more powerful thrust or larger wings with more lift potential. The former solution bears diminishing returns and has in previous configurations been shown to create unnecessary instability with e.g., larger propellers. The latter solution, however, can prove to be a turning-point as the mass of each wing compared to their lifting capabilities is minuscule. On the contrary, the new wings would probably require a more rigid frame or redesigning the drone structure altogether.\\
The wheels have also shown that they currently introduce a large damping offset when the drone is grounded. This issue will play a rather vital role if the drone was to take off directly from the ground.\\
As seen in section \ref{sec:poweruse} the energy usage of the drone is little (compared to the drones mentioned in section \ref{sec:stateoftheart}), but so is the flight time. 
There are numerous reasons for this low flight time and why it easily can be improved:
Firstly, when the drone took off, the ratio between rotational speed and tilt angle was not optimal. Most likely, the drone can take off at a lower rotational speed with the same angle, especially if the size of the wings is increased. This reduces the power used substantially. 
Secondly, when the weight of the drone has been slimmed down, a battery with higher capacity can be mounted. Afterwards, the optimal battery-capacity-to-weight ratio can be found. A fitting ratio will increase the flight time, while still enabling the drone to fly. 
Thirdly, when the size of the wings is increased, the lift generated at the same energy usage will increase. This means that it might even be possible to increase the weight of the drone relative to the current weight and consequently use a battery with larger capacity. 
Implementing all of the above changes should result in a design, which lets the drone fly for far longer periods of time. 

\section{Improving internal communication}\label{sec:communicationimprove}
The drone is, for the time being, fitted to do both I2C and USB communication internally. USB communication was deemed more convenient and fast-enough for the scope of this project.\\
Using polling instead of interrupts could potentially increase the performance of the MPU9250. This would result in more frequent updates of accelerometer and gyroscope data, which might yield better results even though the magnetometer data would be reused in multiple iterations of the filter algorithm. The USB communication could also potentially be improved to reach far higher update frequencies for more accurate data exchange for the control loops (and data analysis). An implementation in a more efficient language like C++ might also be favorable. \\
The primary issue with the USB communication's current implementation is the constant opening and closing of ports. The code could be restructured, such that the ports open when the device starts and only closes when it shuts down. This would greatly minimize the transition period, and thus increase the possible sampling frequency. Another solution is to use I2C. The learning curve for I2C might be at bit steeper than USB, but it can be a faster form of communication in some cases. Furthermore, USB, unlike I2C, has the advantage of no packet loss. 

Though the drone has not needed faster communication for this part of its development, it might need to be improved in the future. 

\section{Additional controllers}
The rotational controller is only the beginning for the regulation of the drone as a system. Two vital controllers need to be implemented in the form of a tilt controller and a height controller. \\
The tilt controller will ensure that the wings and motors work together to maintain a hover condition where the drone is level to the ground. This is crucial for maximizing power and general efficiency.\\
The second controller, the height controller, will be equally necessary, but can, in this case, be built as an extension of the rotational controller with decent approximations of required rotation for hover, descent, and ascent adjusted from the world of helicopter physics. In order for this controller to be realizable, a height sensor of some kind (GPS, sonic, infrared, etc.) must be attached for altitudes below a certain threshold. The drone already has a barometer, but it is not sufficiently accurate to account for the sole altitude estimation, similar to the case of rotational orientation from the IMU used. \\
Lastly, the rotational controller will need to be reconfigured for i.e., gain scheduling to account for the general non-linearity of the drone's behavior. 

\section{From prototype to product}
As of now, this drone is only a proof-of-concept, and as such, it is only a prototype. Therefore, it is both obvious and necessary for future development to build and implement fail-safes into the system such that it does not create hazardous situations for humans and the surroundings. Additionally, keeping the drone in one piece between more and more extensive test flights is desirable. \\
Most importantly these fail-safes will be implemented to eventually take over any safety control, such that its tasks can be automated.\\
The drone's commercial or industrial purposes aren't crystal clear, but some proposed use cases are:
\begin{itemize}
    \item Mobile antenna:
    \begin{itemize}
        \item Weather station
        \item Signal relay
    \end{itemize}
    \item Natural disaster beacon
    \item General surveillance
\end{itemize}

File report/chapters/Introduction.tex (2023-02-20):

%!TEX root = ../Thesis.tex
\chapter{Introduction}\label{chap:introduction}

Autonomous drones have become increasingly important in the field of surveillance and disaster control. However, traditionally designed drones today have a very short flight duration due to their high power usage and high weight (\cite{mavic2}\cite{MG-1}\cite{AutelEvo}). Though these drones cannot stay in the air for long, they can traverse long distances very fast. Such drones can also be configured for carrying heavy payloads because of their powerful motors. However, a drone of such design is not fit for all missions. As the drones are not very efficient, in the sense that while they can have large batteries and strong motors, they have short flight times. There is a need for drones that can carry a small payload, and have very long flight times. These can be useful for local surveillance, mobile cell towers or any type of temporary in-the-air infrastructure.  

The purpose of this project is to analyze an alternate design compared to traditional multirotor drones. This vehicle is an adaptation of a helicopter rotor. Its rotational velocity will create lift from the aerodynamic forces acting upon its wings.

A central processing unit (CPU) will collect sensor data from each wing. The collected data will be analyzed in real-time for further navigation, and control of the drone. This includes the rotational speed.

\section{Objectives}\label{sec:objectives}
In this section, the objectives of the project are defined. Further analysis and design of a solution will be conducted to fulfill these objectives. Analysis will be done in chapter 2, and design as well as review of the results will be done in the subsequent chapters. \\
The proposed solution should:
\begin{itemize}
    \item Control its rotational speed relative to a reference set-point. 
    \item Read sensory data for real-time analysis and log for later use. 
    \item Have full control of and ability to adjust all motors, propeller and servo, of each arm.
    \item Be able to estimate its relative orientation continuously.
\end{itemize}

\subsection{Constraints}
In order to reduce the scope of this project, a few constraints regarding design and project decisions have been made:
\begin{itemize}
    \item Only a simple analysis of aerodynamic challenges will done.
    \item Uncomplicated and easy to implement communication, which might not favor speed and efficiency, will be used. 
    \item Only SISO linear regulators will be considered.
    \item The general core configuration of the drone will not be changed. 
\end{itemize}

\section{Report overview}
\begin{itemize}
    \item \textbf{Chapter 2:} Analysis and definition of the problem for the thesis
    \item \textbf{Chapter 3:} How the drone's hardware and software is restructured. Includes internal communication.
    \item \textbf{Chapter 4:} The implementation and calibration of sensor data within the drone
    \item \textbf{Chapter 5:} Physical analysis and control theory used to approximate the system
    \item \textbf{Chapter 6:} Detailed modelling approach and structure
    \item \textbf{Chapter 7:} Results from measurements on all test setups
    \item \textbf{Chapter 8:} Proposals and ideas for further development and refinement of the drone. This also includes retrospective discussions.
    \item \textbf{Chapter 9:} Conclusion upon project objectives
    \item \textbf{Bibliography:} Bibliography with references used throughout the report
    \item \textbf{Appendix A:} Additional model and system graphics
    \item \textbf{Appendix B:} Link to video of flight test
    \item \textbf{Appendix C:} Test of yaw drift
\end{itemize}

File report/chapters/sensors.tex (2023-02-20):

\chapter{Sensor data and usage} \label{chap:sensordataandusage}%overvej ny titel, måske bare Sensors
This chapter's goal is to explain, in more detail, how the sensor data is utilized most appropriately. 

\section{Compass calibration}
The compass in an IMU is very unstable, though reasonably reliable when at rest, due to the soft and hard iron core distortion caused by varying and permanent magnetic fields surrounding the sensor \cite{magnetometercorrections}. For example, from nearby components on the PCB or the propeller motor.
Therefore, to maximize the stability and precision of the estimations of roll, pitch, and yaw of the drone, the IMU must be calibrated accordingly.
The IMU's magnetometers will be calibrated with the method of Kris Winer\cite{compasscalib}. A well-calibrated compass will output data in a sphere, as small as possible, centered around $[x,y,z]=[0,0,0]$.\\
The calibration routine consists of waving each PCB such that it faces and moves in every direction. Magnetometer measurements are made during the routine to determine its minimum and maximum output values. These values will decide the soft iron core scaling bias.\\
Furthermore, measurements for x, y and z are averaged with the duration of the routine to generate the hard iron core offset biases.\\
Additionally, the factory axis sensitivity adjustment values are read from the compass ROM. \\
An example of realistic measurements from an uncalibrated compass can be seen in fig. \ref{fig:uncalibcompass}. Followingly, example measurements from a calibrated magnetometer are in fig. \ref{fig:calibcompass}.

\begin{figure}[h!]
    \centering
    \begin{minipage}[t]{0.48\textwidth}
        \centering
        
        \caption{Uncalibrated 2D-slice measurements from the magnetometer on \texttt{arm 3}}
        \label{fig:uncalibcompass}
    \end{minipage}%
    \hspace{.03\textwidth}
    \begin{minipage}[t]{0.48\textwidth}
        \centering
        
        \caption{Calibrated 2D-slice measurements from the magnetometer on \texttt{arm 3}}
        \label{fig:calibcompass}
    \end{minipage}
\end{figure} 

\section{Drone orientation}
The orientation of the drone is found by using measurements from the IMU and a sensor fusion algorithm. When working with orientation in 3 dimensions, Euler angles are typically used, but for this application with a continuous rotation object, quaternions are preferred. Euler angles are three angles used to describe the orientation of a rigid body with regards to a fixed coordinate system. The sequence and axis of which the rotations are made, changes the angles, and thus a convention must exist. In aerospace, the most common one is 'Tait-Bryan' angles. It is from this convention that the names roll, pitch and yaw originate. Euler angles are an easy and intuitive way to describe orientation, but have its disadvantages. Further details of Euler angles will not be discussed, only how they fare compared to quaternions. The difference between quaternions and Euler angles will be analyzed, after a brief introduction of quaternions.\\ 

Quaternions are 4-dimensional vectors, with four real coefficients and three imaginary components, typically denoted with i, j, k, usually on the following form:
\begin{equation*}
    \textbf{q} = [q_0, q_1, q_2, q_3] = a + bi + cj + dk
\end{equation*}
where a, b, c, d are real numbers. It can be seen as a scalar \textit{a}, and a three dimensional vector $bi + cj + dk$ . Like regular complex numbers, they can be written on different forms. Quaternions can be used for many things, but are especially useful for describing orientation of 3D objects. When using quaternions for describing rotations, they must be of unit length. When of unit length, the quaternions describe a 3D space on the surface of a hypersphere. Each point on the hypersphere described by a unit quaternion corresponds to a rotation of a 3D object. 
Additional details about quaternions and how they work will not be discussed further, only how they relate to Euler angles.\\

Quaternions are superior to Euler angles for describing rotating objects, especially ones that laps themselves. This is both due to dealing with edge cases like going from 0 to 360 degrees when completing a full rotation, but they also resolve the problem of singularities. Singularities occur with Euler angles when two angles align. This might happen when the second angle moves in such a way that the first and third angle align, losing one degree of freedom. A third benefit is their improved accuracy when integrating over incremental changes in attitude over time \cite{JamesDiebelQuaternions}. \\
%In the control loops for wing tilt, a quaternion based approach will be used, to maintain the benefits compared to traditional Euler angles.\\
As mentioned, when using quaternions to describe rotations, it is essential to note that they are of unit length. The length of a quaternion is found as in equation \ref{eq:normquaternion}. 

\begin{equation} \label{eq:normquaternion}
    ||q|| = \sqrt{q_0^2 + q_1^2 + q_2^2 + q_3^2}
\end{equation}

When converting from unit quaternions to Euler angles, it is crucial to note the sequence of angles. The microcontroller runs a library written by Kris Winer, that utilizes quaternions, such that a stable orientation can be read from the IMU \cite{kriswinermpu9250}. The library implements two filter fusion algorithms: Madgwick and Mahony filters. For converting between quaternions and Euler angles, the library uses 'Tait-Bryan' notation, which also is known as a 1,2,3 sequence \cite{JamesDiebelQuaternions}.
With this notation, the series of calculations is yaw, then pitch, then roll. If the order of rotation is changed, the result is an entirely different set of angles. 

Eq. \ref{eq:uq2ea1}, \ref{eq:uq2ea2} and \ref{eq:uq2ea3} are the equations used by Kris Winer for converting unit quaternions to Euler angles. 
\begin{align} \label{eq:uq2ea1}
      yaw = \psi &= arctan\left(2\cdot (q_1 q_2 + q_0 q_3), \, q_0^2 + q_1^2 - q_2^2 - q_3^2    \right)\\\label{eq:uq2ea2}
    pitch = \theta &= -arcsin\left(  2\cdot(q_1 q_3 -q_0 q_2)   \right)\\
     roll = \phi &= arctan\left( 2\cdot (q_1 q_2 +q_2 q_3), \, q_0^2 -q_1^2 -q_2^2 +q_3^2 \right)\label{eq:uq2ea3}
\end{align}
As noted in the library, for the IMU's coordinate system, positive z-direction is down towards earth, resulting in a positive sign of the gravitational force. With the local declination of the earth's magnetic field taken into account, yaw is the angle between the sensor's x-axis and the true North. 
Pitch is the angle between the sensor's x-axis and the earth's ground plane, towards the earth is positive. Roll is the angle between the sensor's y-axis and the earth's ground plane, towards the earth is negative \cite{kriswinermpu9250}.

As for the filter fusion algorithm, the microcontroller runs Kris Winer's implementation of a Madgwick filter. This filter combines all data from the IMU (accelerometer, gyroscope, and magnetometer) and calculates the unit quaternions that describe the IMU's absolute orientation. 
A Mahony filter was considered, as well. Kris Winer describes the Mahony filter, as similar to the Madgwick filter, but with proportional and integral filtering on the error \cite{quaternionFilters}. This could potentially result in a filter with less drift of values compared to the Madgwick filter. The drone experienced the best performance with the Madgwick filter. This is also supported by at least one source that compared the two \cite{madgwickvsmahony}. The sensitivity of the gyroscope is set to 2000 DPS, which corresponds to approximately six full rotations per second. 
% link: https://x-io.co.uk/open-source-imu-and-ahrs-algorithms/

\section{Chapter summary}
The IMU was calibrated to fit its measurements more accurately to the drone's position. Euler angles and quaternions were introduced, and their pros and cons discussed. Two filter fusion algorithms were presented, as a way of estimating the drone's orientation. The objectives outlined in section \ref{sensorgoals} have been analyzed and are ready to be tested. The performance will be assessed in section \ref{results:measurementprecision}.

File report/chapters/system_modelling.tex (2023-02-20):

\chapter{System modelling}\label{chap:systemmodelling}
For the system modeling, the simplified physics to calculate lift and rotational velocity of the drone from section \ref{sec:preliminaryphysics} will be used. The model is implemented with Simscape Multibody, an add-on of Matlab Simulink.\\

The drone body was developed in Solidworks, seen in fig. \ref{fig:drone3D}. The PCBs, RPi, and battery pack have been assumed as an equal mass distribution on each arm of the drone. As such, they have not been implemented visually in the model.
\begin{figure}[h!]
    \centering
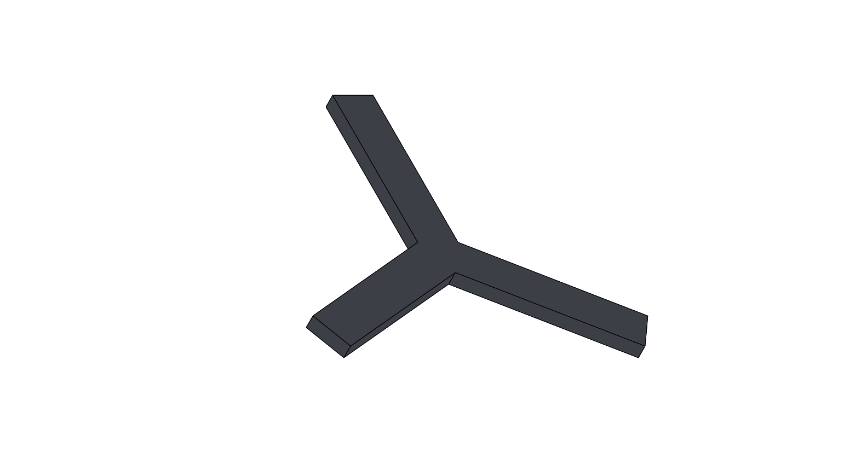
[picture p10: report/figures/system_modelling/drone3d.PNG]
    
    \caption{3D model of the drone's body excluding wings and propeller motors -- constructed in Solidworks}
    \label{fig:drone3D}
\end{figure}
Subsequently, the motors and wings were added to the model to simulate the physical forces acting on the drone. The physics are also implemented using the equations of chapter \ref{sec:preliminaryphysics}. Although for the sake of computational simplicity, the lift is generated by eq. \ref{eq:model_lift}.\\
\begin{equation}
    \label{eq:model_lift}
    L = \frac{1}{2}*A_{wing}*c_L*\rho*\left(\omega*\left(r_{inner}+\frac{L_{wing}}{2}\right)\right)^2
\end{equation}
The wings' drag and lift coefficient are dynamic and thus implemented with a look-up table.\\

The final model is implemented with many subsystems that model different physical properties. The model consists of subsystems for: 
\begin{itemize}[noitemsep]
    \item Wing physics
    \item Motor physics
    \item Coordinate reference
    \item Controller blocks
    \item Measurement facilitation in all of the above
\end{itemize}

The final visual appearance of the modelled drone is shown in fig. \ref{fig:fullmodeldrone}.
\begin{figure}[h!]
    \centering
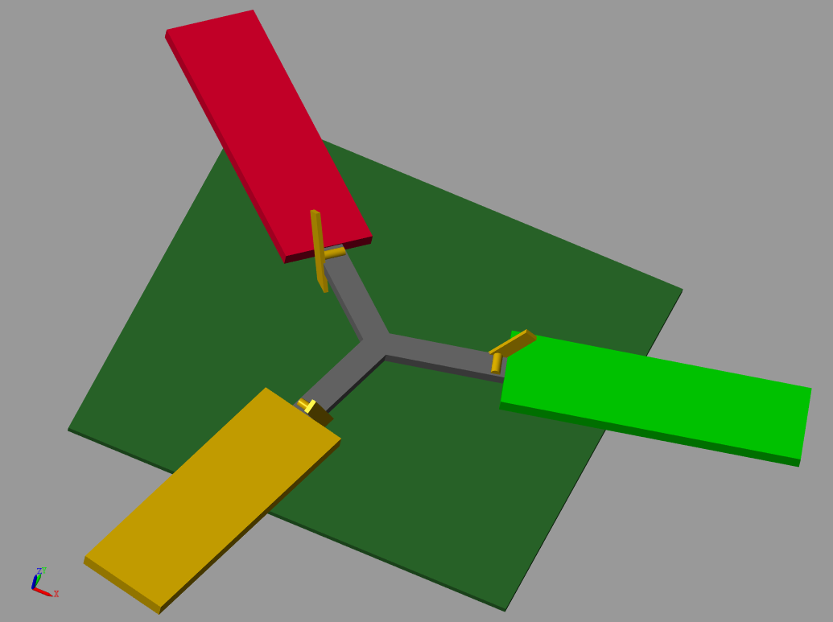
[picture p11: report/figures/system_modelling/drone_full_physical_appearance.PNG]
    
    \caption{The drone model with wings and prop motors}
    \label{fig:fullmodeldrone}
\end{figure}

The top level of the Simulink model can be seen in fig. \ref{fig:toplevelmodel}.

\section{From reality to model and back}
The drag of both motors and wings will be adjusted so that the model fits the real drone's measured data while airborne. \\
The model's natural transfer function will be derived in the same way as with the drone. This is done by stepping the drone at a steady-state. \\

As a result, the model will be used to implement and adjust any proposed rotational controller quickly. Furthermore, it is agile and easy to adjust for changes to the system, or to include new controllers of i.e., height or tilt. The model files are attached to the hand-in.

\section{Chapter summary}
A model of the drone using simplified physics has been implemented using Simscape Multibody in Matlab. The objective outlined in section \ref{modelgoals} has been achieved. Deriving a transfer function and comparing the model with the actual drone will be done in section \ref{sec:modelresponse}.

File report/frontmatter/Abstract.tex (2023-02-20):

%!TEX root = ../Thesis.tex
\chapter{Abstract}
This thesis focuses on building, programming, and controlling a novel type of drone design. The drone behaves like a helicopter rotor as it rotates around its z-axis to create the lift necessary to keep it airborne. The focus is on finishing the drone's basic properties, such as assembling the foundation for a prototype, establishing sensor measurements, form communication between CPU and microcontrollers, and control the drone's rotation. The drone will need to have an estimate of its position in its rotation and be able to control its rotational velocity. The solution is implemented through two tasks: 1) calculating the drone's position with a fusion of sensor data, and 2) analyzing the system to implement a controller. The proposed solution shows that the drone estimates its position with high accuracy at low speeds, but lacks in sampling frequency to maintain this at high rotational velocities. The modeled system is shown to be very similar to the real drone. Finally, the drone is implemented with a PD-controller and feed-forward branch. The controller is successful in regulating the motors' voltage to maintain a specific angular velocity.

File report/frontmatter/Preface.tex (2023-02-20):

%!TEX root = ../Thesis.tex
\chapter{Preface}
This Bachelor's thesis was prepared at the Department of Electrical Engineering at the Technical University of Denmark in fulfillment of the requirements for acquiring a Bachelor of Science degree in Electrical Engineering.

\vfill

\iffalse
{
\centering
    \thesislocation{}, \today\\[1cm]
    %\hspace{3cm}\includegraphics[scale=0.4]{Signature}\\[1cm]
\begin{flushright}
    \thesisauthor{}
\end{flushright}
}
\fi

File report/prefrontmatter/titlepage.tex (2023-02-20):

\calccentering{\unitlength}
\begin{titlingpage}
\thispagestyle{empty}
\sffamily
\vspace*{-2.8cm}
\hfill
\begin{adjustwidth*}{\unitlength}{-\unitlength}
    \begin{adjustwidth}{-0.5cm}{-0.5cm}
		\noindent

		\vspace{\stretch{1}}
		\noindent\textbf{\Huge\ThTitle} \\*[0.2cm]
		\textcolor{dtured}{\rule{\textwidth + 1.5cm}{4pt}}
		\vspace{\stretch{1}} 
		\begin{flushleft}
		\Large
            \ThAuthors\\
            \thesistype{}\\
            \ThYear
        \end{flushleft}
		\vspace{\stretch{2}}
		\noindent
		
		\vspace{\stretch{1}}
		\newline
		\newline
		\newline
		%\noindent
		
		%\vspace{-5cm}
	\end{adjustwidth}
\end{adjustwidth*}
	\cleartoevenpage
		\thispagestyle{empty}
		\ifnum\pdfstrcmp{\ThSubtitle}{}=0 %Check if there is a subtitle
		\noindent\textbf{\ThTitle}
		\else
		\noindent\textbf{\ThTitle, \ThSubtitle}
		\fi
		\vspace{\stretch{1}}

		\noindent\textbf{Report written by:}\\
		\ThAuthors

		\vspace{\stretch{2}}

		\noindent\textbf{Advisor(s):}\\
		\ThSupervisors

		\vspace{\stretch{3}}

		\noindent\ThDepartment

		\vspace{\stretch{4}}

		\noindent\ThElektroEmail

		\vspace{\stretch{5}}
		\frieze
		\noindent{\renewcommand{\arraystretch}{2}\begin{tabular}{@{}lp{0.75\textwidth}}
			Project period:&	\ThProjectPeriod\\
			ECTS:&		\ThECTS\\
			Education:&	\thesistypeabbr\\
			Field:&		\ThField\\
			Class:&		\ThClass\\
			Edition:&	\ThEdition\\
			Remarks:&	\ThRemarks\\
			Copyrights:&\ThCopyrights
		\end{tabular}}
		
\end{titlingpage}
\normalfont
\normalsize

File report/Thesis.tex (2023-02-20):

%!TEX TS-program = xelatex

\input{preamble/static}
\input{preamble/general}
\input{preamble/fonts}
\input{preamble/etc}

\addbibresource{bibliography/Bibliography.bib}

%Program * -> \cdot
\mathcode`\*="8000
{\catcode`\*\active\gdef*{\cdot}}

\begin{document}

\prefrontmatter
\include{prefrontmatter/titlepage}
\clearforchapter

\frontmatter
\include{frontmatter/Abstract}
\include{frontmatter/Preface}
\include{frontmatter/Acknowledgements}
\clearforchapter
\tableofcontents
\pagebreak
\listoffigures*
\listoftables*
\include{chapters/abbreviations}
\clearforchapter

\mainmatter
\include{chapters/Introduction}
%\blinddocument
\include{chapters/analysis}
\include{chapters/communication}
\include{chapters/sensors}
\include{chapters/control_loops}
\include{chapters/system_modelling}
\include{chapters/results}
\include{chapters/future_work}
\include{chapters/Conclusion}

\appendixpage
\appendix
\include{appendices/AnAppendix}

\backmatter
\printbibliography

\cleartoevenpage %To make it look nice.
\include{prefrontmatter/colophon}

\end{document}

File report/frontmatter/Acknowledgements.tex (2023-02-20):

%!TEX root = ../Thesis.tex
\chapter{Acknowledgements}
We want to thank our advisor from DTU Elektro, Associate Professor Jens Christian Andersen, for excellent guidance during this project. Given COVID-19, we were unable to get into a lab for many weeks. He helped us borrow equipment to continue our development elsewhere and later on re-gained us access to the lab. Due to the fact that we inherited the project from our advisor, it was critical that he was available and able to help us get up to speed. \\
Jens Christian Andersen also assisted us a significant amount when we needed new and improved 3D printed parts and obtaining components for the project.

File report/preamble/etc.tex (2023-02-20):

%!TEX root = ../Thesis.tex

% Content specific packages.

\usepackage{rotating}
\usepackage{pdflscape}
\usepackage{blindtext}
\usepackage{algorithm}
\usepackage{algpseudocode}
\usepackage{enumitem}
% Listings
\lstset{
    basicstyle=\footnotesize\ttfamily,% the size of the fonts that are used for the code
    breakatwhitespace=false,          % sets if automatic breaks should only happen at whitespace
    breaklines=true,                  % sets automatic line breaking
    captionpos=b,                     % sets the caption-position to bottom
    commentstyle=\color{s14a},        % comment style
    deletekeywords={},                % if you want to delete keywords from the given language
    escapeinside={\%*}{*)},           % if you want to add LaTeX within your code
    frame=single,                     % adds a frame around the code
    keywordstyle=\bfseries\ttfamily\color{s09}, % keyword style
    language=Python,                  % the language of the code
    morekeywords={*,...},             % if you want to add more keywords to the set
    numbers=left,                     % where to put the line-numbers; possible values are (none, left, right)
    numbersep=5pt,                    % how far the line-numbers are from the code
    numberstyle=\sffamily\tiny\color{dtugray}, % the style that is used for the line-numbers
    rulecolor=\color{dtugray},        % if not set, the frame-color may be changed on line-breaks within not-black text (e.g. comments (green here))
    showspaces=false,                 % show spaces everywhere adding particular underscores; it overrides 'showstringspaces'
    showstringspaces=false,           % underline spaces within strings only
    showtabs=false,                   % show tabs within strings adding particular underscores
    stepnumber=1,                     % the step between two line-numbers. If it's 1, each line will be numbered
    stringstyle=\color{s07},          % string literal style
    tabsize=2,                        % sets default tabsize to 2 spaces
    title=\lstname,                   % show the filename of files included with \lstinputlisting; also try caption instead of title
}

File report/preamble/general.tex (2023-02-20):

	%!TEX root = ../Thesis.tex
\RequirePackage[l2tabu,orthodox]{nag} % Old habits die hard

\newcommand{\papersizeswitch}[3]{\ifnum\strcmp{\papersize}{#1}=0#2\else#3\fi}
\papersizeswitch{b5paper}{\def\classfontsize{10pt}}{\def\classfontsize{12pt}}

\documentclass[\classfontsize,\papersize,twoside,showtrims,extrafontsizes]{memoir}
\RequireXeTeX
\showtrimsoff
\papersizeswitch{b5paper}{
    % Stock and paper layout
    \pagebv
    \setlrmarginsandblock{26mm}{20mm}{*}
    \setulmarginsandblock{35mm}{30mm}{*}
    \setheadfoot{8mm}{10mm}
    \setlength{\headsep}{7mm}
    \setlength{\marginparwidth}{18mm}
    \setlength{\marginparsep}{2mm}
}{
    \papersizeswitch{a4paper}{
        \pageaiv
        \setlength{\trimtop}{0pt}
        \setlength{\trimedge}{\stockwidth}
        \addtolength{\trimedge}{-\paperwidth}
        \settypeblocksize{634pt}{448.13pt}{*}
        \setulmargins{4cm}{*}{*}
        \setlrmargins{*}{*}{0.66}
        \setmarginnotes{17pt}{51pt}{\onelineskip}
        \setheadfoot{\onelineskip}{2\onelineskip}
        \setheaderspaces{*}{2\onelineskip}{*}
    }{
    }
}
\ifnum\strcmp{\showtrims}{true}=0
    % For printing B5 on A4 with trimmarks
    \showtrimson
    \papersizeswitch{b5paper}{\stockaiv}{\stockaiii}
    \setlength{\trimtop}{\stockheight}
    \addtolength{\trimtop}{-\paperheight}
    \setlength{\trimtop}{0.5\trimtop}
    \setlength{\trimedge}{\stockwidth}
    \addtolength{\trimedge}{-\paperwidth}
    \setlength{\trimedge}{0.5\trimedge}
    
    % bigger todos if trim marks
    \setmarginnotes{10pt}{95pt}{\onelineskip}

    \trimLmarks
    
    % put jobname in left top trim mark
    \renewcommand*{\tmarktl}{%
      \begin{picture}(0,0)
        \unitlength 1mm
        \thinlines
        \put(-2,0){\line(-1,0){18}}
        \put(0,2){\line(0,1){18}}
        \put(3,15){\normalfont\ttfamily\fontsize{8bp}{10bp}\selectfont\jobname\ \
          \today\ \ 
          \printtime\ \ 
          Page \thepage}
      \end{picture}}

    % Remove middle trim marks for cleaner layout
    \renewcommand*{\tmarktm}{}
    \renewcommand*{\tmarkml}{}
    \renewcommand*{\tmarkmr}{}
    \renewcommand*{\tmarkbm}{}
\fi

\checkandfixthelayout                 % Check if errors in paper format!
\sideparmargin{outer}                 % Put sidemargins in outer position (why the fuck is this option not default by the class?)

% Large environments
\usepackage{microtype}
\usepackage{mathtools}
\usepackage{listings}                 % Source code printer for LaTeX
\usepackage{tikz}
\setlength{\parskip}{6pt} %Length between paragraphs
% Links
\usepackage[hyphens]{url}             % Allow hyphens in URL's
\usepackage[unicode=false,psdextra]{hyperref}                 % References package

% Graphics and colors
\usepackage{graphicx}                 % Including graphics and using colours
\usepackage{xcolor}                   % Defined more color names
\usepackage{eso-pic}                  % Watermark and other bag
\usepackage{textpos}					 % For textblock use
\usepackage{setspace}				 % Spacing environment
\usepackage{preamble/dtucolors}	
\graphicspath{{graphics/}}

% float barriers and no indent
\usepackage{placeins}
\setlength\parindent{0pt}

% Language
\usepackage{polyglossia}    % multilingual typesetting and appropriate hyphenation
\setdefaultlanguage{english}
\usepackage{csquotes}       % language sensitive quotation facilities

%\DisemulatePackage{tocbibind}
%\usepackage[nottoc]{tocbibind}

% Bibliography (references)
\usepackage[backend=biber,
            style=alphabetic,
            %backref=true,
            abbreviate=false,
            dateabbrev=false,
            alldates=long]{biblatex}

% Floating objets, captions and references
\usepackage{flafter}  % floats is positioned after or where it is defined! 
%\setfloatlocations{figure}{bhtp}   % Set floats for all figures
%\setfloatlocations{table}{bhtp}    % Set floats for all tables
%\setFloatBlockFor{section}         % Typeset floats before each section
\usepackage[noabbrev,nameinlink,capitalise]{cleveref} % Clever references. Options: "fig. !1!" --> "!Figure 1!"
\hangcaption
\captionnamefont{\bfseries}
\subcaptionlabelfont{\bfseries}
\newsubfloat{figure}
\newsubfloat{table}
%\letcountercounter{figure}{table}         % Consecutive table and figure numbering
%\letcountercounter{lstlisting}{table}     % Consecutive table and listings numbering
\captiontitlefinal{.}
% strip things from equation references, making them "(1)" instead of "Equation~1"
% from http://tex.stackexchange.com/questions/122174/how-to-strip-eq-from-cleveref
\crefformat{equation}{(#2#1#3)}
\crefrangeformat{equation}{(#3#1#4) to~(#5#2#6)}
\crefmultiformat{equation}{(#2#1#3)}%
{ and~(#2#1#3)}{, (#2#1#3)}{ and~(#2#1#3)}

% Table of contents (TOC)
\setcounter{tocdepth}{1}              % Depth of table of content
\setcounter{secnumdepth}{2}           % Depth of section numbering
\setcounter{maxsecnumdepth}{3}        % Max depth of section numbering

% Todos
\usepackage{totcount}                 % For total counting of counters
\def\todoshowing{}
\ifnum\strcmp{\showtodos}{false}=0
    \def\todoshowing{disable}
\fi
\usepackage[colorinlistoftodos,\todoshowing]{todonotes} % Todonotes package for nice todos
\newtotcounter{todocounter}           % Creates counter in todo
\let\oldtodo\todo
\newcommand*{\newtodo}[2][]{\stepcounter{todocounter}\oldtodo[#1]{\thesection~(\thetodocounter)~#2}}
\let\todo\newtodo
\let\oldmissingfigure\missingfigure
\newcommand*{\newmissingfigure}[2][]{\stepcounter{todocounter}\oldmissingfigure[#1]{\thesection~(\thetodocounter)~#2}}
\let\missingfigure\newmissingfigure
\makeatletter
\newcommand*{\mylistoftodos}{% Only show list if there are todos
\if@todonotes@disabled
\else
    \ifnum\totvalue{todocounter}>0
        \markboth{\@todonotes@todolistname}{\@todonotes@todolistname}
        \phantomsection\todototoc
        \listoftodos
    \else
    \fi
\fi
}
\makeatother
\newcommand{\lesstodo}[2][]{\todo[color=green!40,#1]{#2}}
\newcommand{\moretodo}[2][]{\todo[color=red!40,#1]{#2}}

% Chapterstyle
\makeatletter
\makechapterstyle{mychapterstyle}{
    \chapterstyle{default}
    \def\format{\normalfont\sffamily}

    \setlength\beforechapskip{0mm}

    \renewcommand*{\chapnamefont}{\format\HUGE}
    \renewcommand*{\chapnumfont}{\format\fontsize{54}{54}\selectfont}
    \renewcommand*{\chaptitlefont}{\format\fontsize{42}{42}\selectfont}

    \renewcommand*{\printchaptername}{\chapnamefont\MakeUppercase{\@chapapp}}
    \patchcommand{\printchaptername}{\begingroup\color{dtugray}}{\endgroup}
    \renewcommand*{\chapternamenum}{\space\space}
    \patchcommand{\printchapternum}{\begingroup\color{dtured}}{\endgroup}
    \renewcommand*{\printchapternonum}{%
        \vphantom{\printchaptername\chapternamenum\chapnumfont 1}
        \afterchapternum
    }

    \setlength\midchapskip{1ex}

    \renewcommand*{\printchaptertitle}[1]{\raggedleft \chaptitlefont ##1}
    \renewcommand*{\afterchaptertitle}{\vskip0.5\onelineskip \hrule \vskip1.3\onelineskip}
}
\makeatother
\chapterstyle{mychapterstyle}

% Header and footer
\def\hffont{\sffamily\small}
\makepagestyle{myruled}
\makeheadrule{myruled}{\textwidth}{\normalrulethickness}
\makeevenhead{myruled}{\hffont\thepage}{}{\hffont\leftmark}
\makeoddhead{myruled}{\hffont\rightmark}{}{\hffont\thepage}
\makeevenfoot{myruled}{}{}{}
\makeoddfoot{myruled}{}{}{}
\makepsmarks{myruled}{
    \nouppercaseheads
    \createmark{chapter}{both}{shownumber}{}{\space}
    \createmark{section}{right}{shownumber}{}{\space}
    \createplainmark{toc}{both}{\contentsname}
    \createplainmark{lof}{both}{\listfigurename}
    \createplainmark{lot}{both}{\listtablename}
    \createplainmark{bib}{both}{\bibname}
    \createplainmark{index}{both}{\indexname}
    \createplainmark{glossary}{both}{\glossaryname}
}
\pagestyle{myruled}
\copypagestyle{cleared}{myruled}      % When \cleardoublepage, use myruled instead of empty
\makeevenhead{cleared}{\hffont\thepage}{}{} % Remove leftmark on cleared pages

\makeevenfoot{plain}{}{}{}            % No page number on plain even pages (chapter begin)
\makeoddfoot{plain}{}{}{}             % No page number on plain odd pages (chapter begin)

% \*section, \*paragraph font styles
\setsecheadstyle              {\huge\sffamily\raggedright}
\setsubsecheadstyle           {\LARGE\sffamily\raggedright}
\setsubsubsecheadstyle        {\Large\sffamily\raggedright}
%\setparaheadstyle             {\normalsize\sffamily\itseries\raggedright}
%\setsubparaheadstyle          {\normalsize\sffamily\raggedright}

% Hypersetup
\hypersetup{
    pdfauthor={\ThAuthors{}},
    pdftitle={\ThTitle{}},
    pdfsubject={\ThSubtitle{}},
    pdfdisplaydoctitle,
    bookmarksnumbered=true,
    bookmarksopen,
    breaklinks,
    linktoc=all,
    plainpages=false,
    unicode=true,
    colorlinks=false,
    citebordercolor=dtured,           % color of links to bibliography
    filebordercolor=dtured,           % color of file links
    linkbordercolor=dtured,           % color of internal links (change box color with linkbordercolor)
    urlbordercolor=s13,               % color of external links
    hidelinks,                        % Do not show boxes or colored links.
}
% Hack to make right pdfbookmark link. The normal behavior links just below the chapter title. This hack put the link just above the chapter like any other normal use of \chapter.
% Another solution can be found in http://tex.stackexchange.com/questions/59359/certain-hyperlinks-memoirhyperref-placed-too-low
\makeatletter
\renewcommand{\@memb@bchap}{%
  \ifnobibintoc\else
    \phantomsection
    \addcontentsline{toc}{chapter}{\bibname}%
  \fi
  \chapter*{\bibname}%
  \bibmark
  \prebibhook
}
\let\oldtableofcontents\tableofcontents
\newcommand{\newtableofcontents}{
    \@ifstar{\oldtableofcontents*}{
        \phantomsection\addcontentsline{toc}{chapter}{\contentsname}\oldtableofcontents*}}
\let\tableofcontents\newtableofcontents
\makeatother

% Confidential
\newcommand{\confidentialbox}[1]{
    \put(0,0){\parbox[b][\paperheight]{\paperwidth}{
        \begin{vplace}
            \centering
            \scalebox{1.3}{
                \begin{tikzpicture}
                    \node[very thick,draw=red!#1,color=red!#1,
                          rounded corners=2pt,inner sep=8pt,rotate=-20]
                          {\sffamily \HUGE \MakeUppercase{Confidential}};
                \end{tikzpicture}
            }
        \end{vplace}
    }}
}

% Prefrontmatter
\newcommand{\prefrontmatter}{
    \pagenumbering{alph}
    \ifnum\strcmp{\confidential}{true}=0
        \AddToShipoutPictureBG{\confidentialbox{10}}   % 10% classified box in background on each page
        \AddToShipoutPictureFG*{\confidentialbox{100}} % 100% classified box in foreground on first page
    \fi
}

% DTU frieze
\newcommand{\frieze}{%
    \AddToShipoutPicture*{
        \put(0,0){
            \parbox[b][\paperheight]{\paperwidth}{%
                
                \vspace*{2.5cm}
            }
     }
    }
}

% This is a double sided book. If there is a last empty page lets use it for some fun e.g. the frieze.
% NB: For a fully functional hack the \clearpage used in \include does some odd thinks with the sequence numbering. Thefore use \input instead of \include at the end of the book. If bibliography is used at last everything should be ok.
\iffalse
\makeatletter
% Adjust so gatherings is allowd for single sheets too! (hacking functions in memoir.dtx)
\patchcmd{\leavespergathering}{\ifnum\@memcnta<\tw@}{\ifnum\@memcnta<\@ne}{
    \leavespergathering{1}
    % Insert the frieze
    \patchcmd{\@memensuresigpages}{\repeat}{\repeat\frieze
    \vspace{\fill}
    
    \sffamily
    \noindent\ThDepartmentBack
    \vspace*{2.5cm}
    }{}{}
}{}
\makeatother
\fi
% Solution to microtype package warnings when using xelatex and microtype older than version 2.7
% The solution was found at:
% https://tex.stackexchange.com/questions/373594/microtype-producing-dozens-of-unknown-slot-number-warnings
\makeatletter
\def\MT@is@composite#1#2\relax{%
  \ifx\\#2\\\else
    \expandafter\def\expandafter\MT@char\expandafter{\csname\expandafter
                    \string\csname\MT@encoding\endcsname
                    \MT@detokenize@n{#1}-\MT@detokenize@n{#2}\endcsname}%
    % 3 lines added:
    \ifx\UnicodeEncodingName\@undefined\else
      \expandafter\expandafter\expandafter\MT@is@uni@comp\MT@char\iffontchar\else\fi\relax
    \fi
    \expandafter\expandafter\expandafter\MT@is@letter\MT@char\relax\relax
    \ifnum\MT@char@ < \z@
      \ifMT@xunicode
        \edef\MT@char{\MT@exp@two@c\MT@strip@prefix\meaning\MT@char>\relax}%
          \expandafter\MT@exp@two@c\expandafter\MT@is@charx\expandafter
            \MT@char\MT@charxstring\relax\relax\relax\relax\relax
      \fi
    \fi
  \fi
}
% new:
\def\MT@is@uni@comp#1\iffontchar#2\else#3\fi\relax{%
  \ifx\\#2\\\else\edef\MT@char{\iffontchar#2\fi}\fi
}
\makeatother

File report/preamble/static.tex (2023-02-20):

%!TEX root = ../Thesis.tex

% This information is used in titlepage, colophon, preface and hyperref setup (pdf metainfo), and other options.

%\def\thesistypeabbr{B.Eng.}
%\def\thesistype    {Bachelor of Engineering}
\def\thesistypeabbr{B.Sc.Eng.}
\def\thesistype    {Bachelor of Science in Engineering}
%\def\thesistypeabbr{M.Sc.}
%\def\thesistype    {Master of Science in Engineering}
%\def\thesistypeabbr{Ph.D.}
%\def\thesistype    {Doctor of Philosophy}

\def\papersize    {a4paper} % Final papersize (b5paper/a4paper), recommended papersize for DTU Compute is b5paper
\def\showtrims    {false} % Print on larger paper than \papersize and show trim marks (true/false)?

\def\showtodos    {false}  % Show todos (true/false)?
\def\confidential {false} % Confidential thesis (true/false)?

\def\ThYear{2020}

\def\ThTitle{Design of Flying Propeller}
\def\ThSubtitle{}

\def\ThAuthors{Andreas Grønbech Petersen (s173901) \\ Jonas Brøndum (s173952)}
\def\Owner{Andreas Grønbech Petersen \& Jonas Brøndum} % Used for copyright
\def\ThSupervisors{Jens Christian Andersen, Associate Professor at the Electrical Engineering Department of DTU}
\def\ThDepartment{\textbf{DTU Electrical Engineering }\\ Technical University of Denmark \\ 2800 Kgs. Lyngby\\ Denmark}

\def\ThDepartmentBack{\textbf{DTU Electrical Engineering \\ Department of Electrical Engineering }\\ Technical University of Denmark \\ \\ Ørsteds Plads \\ Building 348 \\ DK-2800 Kgs. Lyngby \\ Denmark \\ Tel: (+45) 45 25 38 00 \\ \\ www.elektro.dtu.dk}

\def\ThElektroEmail{elektro@elektro.dtu.dk}
\def\ThBeginDate{17th of February}
\def\ThEndDate{29th of June}
\def\ThProjectPeriod{\ThBeginDate - \ThEndDate}
\def\ThECTS{15}
\def\ThField{Electrical Engineering}
\def\ThClass{Public}
\def\ThEdition{1. edition}
\def\ThRemarks{This report is submitted as partial fulfillment of the requirements for graduation in the above education at the Technical University of Denmark.}
\def\ThCopyrights{\copyright \Owner, \ThYear}

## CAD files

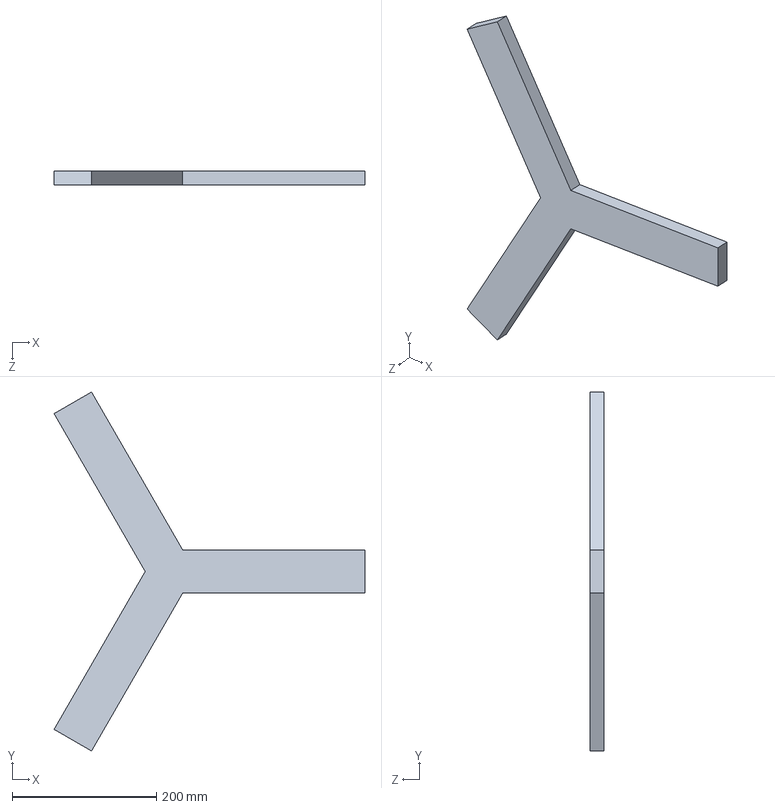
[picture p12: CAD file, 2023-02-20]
drone_3d_model/drone3d.SLDPRT
431.0 x 497.7 x 20.0 mm

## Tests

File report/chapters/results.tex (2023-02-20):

\chapter{Results}\label{chap:results}
The goal of this chapter is to test the proposed solutions mentioned in the previous chapters and review their performance. 
\section{Test setups}
Two different test setups are used when assessing the performance of the drone. One setup for testing on the ground, and one setup for simulating in-air behaviour. 

\subsection{Ground}
The ground test rig consists of a rod that the drone can rotate about, to minimize unwanted behavior. The first iteration can be seen in fig. \ref{fig:testsetup_ground}. For the second iteration, a large sheet of wood for the drone to rotate on was added to reduce friction from the surface. The rod material was changed from aluminum to carbon fiber to reduce magnetic disturbances.
\begin{figure}[h]
    \centering
    
    \caption{First iteration of the test setup on ground, prior to the second and more stable version of this setup}
    \label{fig:testsetup_ground}
\end{figure}

When estimating the orientation of the drone, a compass rose was put in between the drone and the sheet of wood. North on the compass rose was aligned with true north by use of a compass on a smartphone. 

This setup was used to test measurement precision and derive a transfer function for the system on the ground. 

During the first round of tests, the drone's center module collapsed (see fig. \ref{fig:dronecollapse}). Therefore, a new, more rigid, and sturdy center module was 3D printed.

\begin{figure}[h]
    \centering
    
    \caption{Close-up of collapsed center module of the drone after an early test run}
    \label{fig:dronecollapse}
\end{figure}
\FloatBarrier

\subsection{"In-air"}
In this setup (see fig. \ref{fig:testsetup_air}), the drone is suspended from the wooden beam by a thin cord. This cord is so thin that it can easily rotate many times about itself without breaking. Between the cord and the beam, a suitcase-scale is attached. The scale will measure how much lift the drone can generate. The wooden beam is attached to the solid post seen to the left with a rope. 
This setup frees the drone from any friction that was introduced by the wheels. 

This setup was used for wing estimations, getting a transfer function for the system in the air, and testing control loops. 

\begin{figure}[h]
    \centering
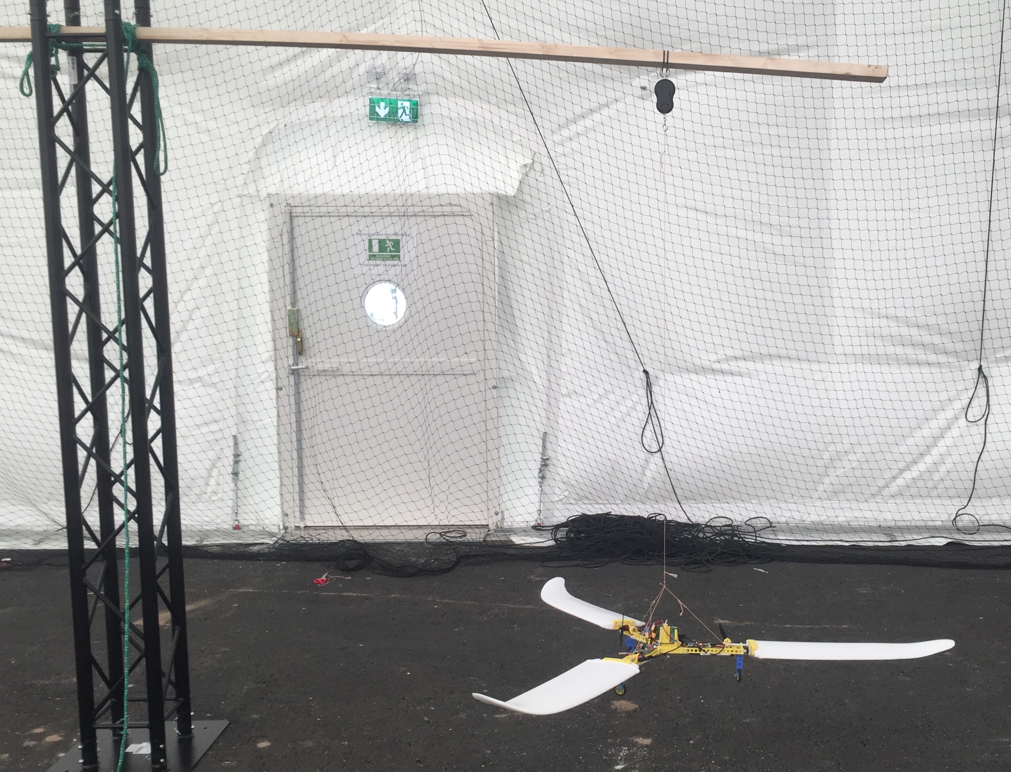
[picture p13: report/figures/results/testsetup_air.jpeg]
    
    \caption{Test setup, air. The drone is hanging from a wooden beam in a cord to simulate in-air behavior}
    \label{fig:testsetup_air}
\end{figure}

\section{Measurement precision}\label{results:measurementprecision}
The precision of the sensor data is crucial for implementing and maintaining reliable controllers on the drone. Thereafter, both the angular velocity and orientation estimations received from the drone are analyzed. 

\subsection{Angular velocity}
The drone's angular velocity sensing is tested by rotating the drone at a constant speed. The rotation is recorded with a video camera and analyzed on a computer. The velocity is tested at PWM of 45\% and 60\% using the ground setup. A comparison of the gathered and recorded data will be made. In this comparison, the measurement of rotational velocity will be converted to rotations per second, because it is challenging to read rotation in radians per second from a video. 

The results of the analysis can be seen in fig. \ref{fig:RPS45PWM} and \ref{fig:RPS60PWM}. 
\begin{figure}[h!]
    \centering
    \begin{minipage}[t]{0.48\textwidth}
        \centering
        
    \caption{Rotations per second for PWM at 45\% on ground. Purple dots are from video analysis}
    \label{fig:RPS45PWM}
    \end{minipage}%
    \hspace{.03\textwidth}
    \begin{minipage}[t]{0.48\textwidth}
        \centering
        
    \caption{Rotations per second for PWM at 60\% on ground. Purple dots are from video analysis}
    \label{fig:RPS60PWM}
    \end{minipage}
\end{figure} 
\FloatBarrier
The three lines seen on the figures are each arm's measurement of angular velocity converted to rotations per second. The dots are the rotational speed of the drone derived from the video. Each rotation after the drone started is found and plotted. The start of the recording and start of the drone is lined up as best as possible.

Visually, the distance between points and fits looks very low, especially for PWM at 45\%. The mean square error of the points from the video compared to the sensor data is found to be $MSE_{PWM=45\%} = 6.8220\cdot 10^{-5}$ and $MSE_{PWM=60\%} = 1.8*10^{-3}$. From this it can be concluded, that the measurements of rotational velocity are precise and work as expected.

\subsection{Orientation estimation}
The orientation of the drone is described by roll, pitch, and yaw.  The magnetometer on the drone has been corrected for the local declination of the magnetic field. With the correction, yaw measures the angle from the IMU's x-axis to the true north. 
The ground test-setup was used to examine the drone's ability to estimate its orientation. 
While the drone was rotating, it was recorded from an angle directly above it. This was done for PWM at 40\% and 50\%. 

Continuous measurement of yaw with data from all arms can be seen in fig. \ref{fig:rpm40woodallarms}. 

\begin{figure}[h]
    \centering
    
    \caption{Yaw measurements, PWM at 40\% on ground test setup}
    \label{fig:rpm40woodallarms}
\end{figure}
As can be seen, there are about 110 degrees between all arms most of the time. 
The angle doesn't always go all the way to 0 or to 360, but this is also visually exaggerated due to the cyclic nature of angles. Errors related to this will be discussed in section \ref{error_measurementprecision}.

In the analysis of the videos, it was noted each time \texttt{arm 1} had rotated 90 degrees. These points are plotted against \texttt{arm 1's} measurement of the yaw angle. This was done both for RPM at 40\% and 50\% (see fig \ref{fig:rpm40woodvid} and \ref{fig:rpm50woodvid}). 
\begin{figure}[h!]
    \centering
    \begin{minipage}[t]{0.48\textwidth}
        \centering
        
        \caption{Yaw measuremnets, PWM at 40\% on ground test setup, arm 1 and video}
    \label{fig:rpm40woodvid}
    \end{minipage}%
    \hspace{.03\textwidth}
    \begin{minipage}[t]{0.48\textwidth}
        \centering
        
        \caption{Yaw measurements, PWM at 50\% on ground test setup, arm 1 and video}
        \label{fig:rpm50woodvid}
    \end{minipage}
\end{figure} 
Angles of either 0 or 360 degrees from the video analysis, are always plotted as 0 degrees for clarity.
At a PWM of 40 \%, the measured data agree quite well with the video analysis. At higher levels of PWM, the plot starts to lack some data points in the rotation. 

Locating north within $\pm 1$ degrees was never the target goal. A well-calibrated IMU with a Madgwick filter can have a precision of $\pm 4$ degrees \cite{FilterFusionPrecision}. This test shows that it is possible to measure with an accuracy of $\pm 20$ degrees when rotating continuously.  

For the time being, it is somewhat unreliable for higher speeds, but it would be easy to improve (see chapter \ref{sec:communicationimprove}).
Sources of errors and other limitations are discussed in section \ref{error_measurementprecision}.

\subsection{Sources of error} \label{error_measurementprecision}
The general increase in error between video and measured data can be attributed to several things. 
Firstly, due to not having an infinitely high sampling rate on the microcontrollers and its sensors, the error in measurements will naturally increase as the rotational speed increases. 
The sampling rate of the IMU is 100 Hz for the magnetometer, 200 Hz for the gyroscope, and about 1 kHz for the accelerometer. As mentioned previously, the IMU is configured for interrupt-based communication. This limits the update frequency to the lowest common denominator and therefore is 100 Hz. 

Secondly, the video recording was limited to 30 fps. As the picture becomes increasingly blurry, the observer's inability to distinguish angles expectedly grows. The error between the points from the video and the measurements will also increase with velocity. 

Finally, the plots may also make the data look worse than it is. Given that the update frequency only is 30 Hz between RPi and microcontroller, significant data is lost. About 2/3 of all data points are never seen on the RPi, which might explain the lack of "complete rotations" seen in fig. \ref{fig:rpm50woodvid}. At times, the data jumps from 200-300 degrees down to a value slightly above 0 degrees. These jumps are  likely caused by a lack of data on the RPi, rather than lack of data on the microcontroller.

A test of yaw drift can be seen in appendix \ref{fig:yawdrifttest}. It shows no noteworthy drift. 

\section{Wing estimations} \label{chap:wing_est}
The wings' properties were measured with the "in-air" setup. The motors had a constant input voltage, $V_{in} = 3.57 V$ corresponding to a PWM of 30\%. Afterwards, the lift and angular velocity for a varying wing pitch was measured to estimate both the lift and drag coefficients.\\
The lift was measured as a mass with the suitcase-scale on the end of the string carrying the drone. The final lift and angular velocity versus wing pitch can be seen in fig. \ref{fig:lift_omega_measured}.

\begin{figure}[h]
    \centering
    
    \caption{Lift and angular velocity measured for different wing pitches}
    \label{fig:lift_omega_measured}
\end{figure}

The lift coefficient was estimated from the approach in eq. \ref{eq:cLestimation}. The approach is similar to the one used to calculate the required rotation in eq. \ref{eq:omega_approx}. N is the amount of iterations (here $N=10.000$) and $\Delta R = L_{wing}/N$.
\begin{equation}
\label{eq:cLestimation}
    c_L(\theta) = \frac{1}{3} * \frac{L_{meas}(\theta)*N}{\rho*A_{wing}*\omega^2*\sum_{i=1}^{N} (r_{inner}+ i*\Delta R)^2}
\end{equation}
The comparison of the estimated and measured lift can be seen in fig. \ref{fig:lift_measured}.\\

The drag coefficient at a wing pitch of 0 degrees was adjusted in the Matlab-model until simulations showed similar physical properties to the ones of the drone. This was achieved at a drag coefficient of, $c_{Dbase} = 0.176$ and angular velocity of $\omega_{base} = 15.4 [rad/s]$.\\ 
The subsequent drag coefficients were estimated with eq. \ref{eq:drag_estimation}, since the output power of the motors were the same throughout the test.
\begin{equation}
\label{eq:drag_estimation}
    c_D(\theta) = \left(\frac{\omega_{base}}{\omega_{\theta}}\right)^2* c_{dBase}
\end{equation}
The resulting drag coefficients can be seen compared to the Foil Sim Applet's estimation in fig. \ref{fig:drag_measured}. Furthermore, measured lift coefficients compared to Foil Sim Applet's estimation can be seen in fig \ref{fig:lift_measured}.\\
Both the drag and lift coefficients measured deviate significantly from the ones obtained from the applet. This can be partially explained by the imprecise scale (meant for weighing suitcases) and the fact that the drone does oscillate slightly away from directly underneath the string. These results are prone to many errors caused by a series of underlying approximations and assumptions. The complexity of aerodynamics shall not be underestimated; however, these results work decently for testing purposes.

\begin{figure}[h!]
    \centering
    \begin{minipage}[t]{0.48\textwidth}
        \centering
        
    \caption{Lift coefficient measured with the test rig compared to the estimated lift coefficient from the Foil Sim Applet}
    \label{fig:lift_measured}
        
    \end{minipage}%
    \hspace{.03\textwidth}
    \begin{minipage}[t]{0.48\textwidth}
        \centering
        
    \caption{Drag coefficient measure estimation with the test rig compared to the coefficients from the Foil Sim Applet}
    \label{fig:drag_measured}
    \end{minipage}
\end{figure} 
Fig. \ref{fig:LDratio_measured} is a plot of the lift-to-drag ratio measurement and Foil Sim estimation.
\begin{figure}[h]
    \centering
    
    \caption{Lift-to-drag ratio as measured and estimated with the Foil Sim Applet}
    \label{fig:LDratio_measured}
\end{figure}
\newpage

\section{Rotation controller and system response}\label{results:rotcontroller}
Transfer functions will be derived for the system in three different states and one for the model. First state is a grounded system. Second state is in the air with minimal drag. Third state is in the air with some drag. The functions will be analyzed and compared to each other, to examine the difference between states as well as model compared to the real world. 
Eventually the final controller will be derived and implemented. 

\subsection{Deriving transfer functions}
To derive a transfer function, the theory in section \ref{tf_teori} is used. The system received a step of PWM from 35\% to 39\%, and is analysed both on the ground and in the air. This value interval might seem arbitrary, but was chosen, as it is high enough to let the drone rotate both on the ground and in the air, yet low enough so the drone is easily observable. Furthermore, in the air, it is stepped both with minimal drag and some drag. This was chosen to investigate if there was any notable difference between the system responses in the three cases. 
% When using System Identification Toolbox, a guess of a system with 1 pole and 2 poles are made. This is due to having a low sampling frequency, so time constants from the motors and other really fast components are not visible. One constant is expected from the inertia of the drone due to its size, and one for 

\subsubsection{Grounded system}
The step from PWM of 35 \% to 39\% is made using the ground test-setup and can be seen in fig. \ref{fig:stepwood}.
\begin{figure}[h!]
    \centering
    \begin{minipage}[t]{0.48\textwidth}
        \centering
        
        \caption{Step on wooden surface using the ground test-setup}
        \label{fig:stepwood}
    \end{minipage}%
    \hspace{.03\textwidth}
    \begin{minipage}[t]{0.48\textwidth}
        \centering
        
        \caption{Plot from System Identification Toolbox. $Tf_1$ is 1 pole, $Tf_2$ is two poles. The data was offset to start in 0}
        \label{fig:stepwoodsysid}
    \end{minipage}
\end{figure} 
This looks quite similar to a 1st or 2nd order system. One might expect a system with more poles, but with the low sampling frequency smaller time constants (e.g. electrical) cannot be measured. \\
Assuming a 1st order system and analysing the step, the time constant is found as $\tau_1 = 1.6404$. The pole is $p_1 = -0.6096$. \textit{b} can then be calculated:

\begin{equation}
    b = \frac{y_{final} - y_{init}}{x_{final}}* a =  \frac{1.89-0.71}{4.5} \cdot 0.6096 = 0.1603
\end{equation}

The manually derived transfer function becomes:
\begin{equation}\label{eq:woodsysman}
    tf_{manual} = \frac{0.1603}{s+0.6096}
\end{equation}

Analysing the step with System Identification Toolbox, the following step and transfer functions are derived, see fig. \ref{fig:stepwoodsysid} as well as eq. \ref{eq:woodsysid1} and \ref{eq:woodsysid2}. 

\begin{equation}\label{eq:woodsysid1}
    tf_1 = \frac{0.1387}{s+0.5383}
\end{equation}
\begin{equation}\label{eq:woodsysid2}
    tf_2 = \frac{0.03641}{s^2 + 0.6571 s + 0.1462}
\end{equation}
The transfer function found manually in eq. \ref{eq:woodsysman} and the two found with System Identification Toolbox, are very similar. The two 1st order systems have poles in approximately the same places and almost the same gain. 
The 2nd order system has a complex pole pair located at $-3.29 \pm 0.196 I$. The complex poles are presumably caused by either flex in the wheel mounting, or due to the vibration introduced from the wooden surface. 

\subsubsection{Airborne system with minimal drag}\label{sec:airminimal}
The step of the system was made with the air test-setup, see fig. \ref{fig:steprope}.
\begin{figure}[h!]
    \centering
    \begin{minipage}[t]{0.48\textwidth}
        \centering
        
        \caption{Step using air test-setup}
        \label{fig:steprope}
    \end{minipage}%
    \hspace{.03\textwidth}
    \begin{minipage}[t]{0.48\textwidth}
        \centering
        
        \caption{Plot from System Identification Toolbox, $Tf_1$ is 1 pole, $Tf_2$ is 2 poles. The data was offset to start in 0}
        \label{fig:stepropesysid}
    \end{minipage}
\end{figure} 

Analyzing the step with System Identification Toolbox, the fits can be seen in fig. \ref{fig:stepropesysid}, and transfer functions in eq. \ref{eq:airsysid1} and \ref{eq:airsysid2}.

\begin{equation}\label{eq:airsysid1}
    Tf_1 = \frac{0.1132}{s+0.3523}
\end{equation}
\begin{equation}\label{eq:airsysid2}
    Tf_2 = \frac{0.4608}{s^2 + 4.439s+1.434}
\end{equation}
The first pole for the 1st order and 2nd order system is practically identical at respectively $-0.3523$ and $-0.3507$. Due to its very low frequency, this pole probably correlates to the inertia of the drone. \\
The second pole for the 2nd order system is at $-4.088$, and corresponds to a very small time constant. The second, less dominant, pole might possibly be the pole associated with the mechanical time constant of the motors \cite{motordata} (see also section \ref{sec:modelresponse}) .

\subsubsection{Airborne system with more drag}
The step was made using the air test-setup, but this time with a 5 degrees tilt of the wings (positive angles creates lift). The step response can be seen fig. \ref{fig:steprope65}.

\begin{figure}[h!]
    \centering
    \begin{minipage}[t]{0.48\textwidth}
        \centering
        
        \caption{Step using air test-setup with a pitch angle of $\sim$5 degrees}
        \label{fig:steprope65}
    \end{minipage}%
    \hspace{.03\textwidth}
    \begin{minipage}[t]{0.48\textwidth}
        \centering
        
        \caption{Plot from System Identification Toolbox, $Tf_1$ is 1 pole, $Tf_2$ is 2 poles. The data was offset to start in 0. Pitch angle was $\sim$5 degrees}
        \label{fig:steprope65sysid}
    \end{minipage}
\end{figure} 

With System Identification Toolbox, the following fits and transfer functions are found, see fig. \ref{fig:steprope65sysid} as well as eq. \ref{eq:air65sysid1} and \ref{eq:air65sysid2}. 

\begin{equation}\label{eq:air65sysid1}
    Tf_1 = \frac{0.1311}{s+0.8044}
\end{equation}
\begin{equation}\label{eq:air65sysid2}
    Tf_2 = \frac{3.862}{s^2 + 29.91s + 23.7}
\end{equation}
The 2nd order system's poles are real and located at $p_1=-0.815$ and $p_2=-29.095$. The first pole from the 2nd order system is very close to the pole from the 1st order system. This second pole is much smaller than the second pole for the case with minimal drag. This clearly outlines some nonlinear component in the system and may very well be caused by the drag. 

\subsubsection{Comparison of systems}
The systems on wheels and in the air are very similar in terms of time constants, but the resistance from rolling associated with the wheels create a large offset. With a PWM of 35\%, the angular velocity in the air is about 16 rad/s, but on the ground, it is approximately 0.8 rad/s. This is a massive loss in rotational energy. Furthermore, the absolute increase in amplitude for the steps on the ground and in the air is about the same, which means the rolling resistance does not increase appreciably with angular velocity. \\ 
The dominating time constant for the case with some drag is faster than the one with minimal drag, but the system also reaches a far lower amplitude. The minimal drag case's relative increase in amplitude is 1.5 but is only 0.75 for the case with some drag. Due to non-linear components, there is a notable difference between the two step-responses, both in terms of steady-state error and pole placement. This can be solved with gain scheduling, though this concept will not be explored further in this thesis. 

\subsection{Modelled system's response}\label{sec:modelresponse}
The model transfer function was derived in a similar fashion to the method above. At a steady state rotation the input voltage of $V_{in} = 0.35*11.9V = 4.17 \,V$ was stepped to $V_{in} = 0.39*11.9V = 4.641\,$. The model's step response was analyzed with the help of the Tfest-function in the System Identification's Toolbox (fig. \ref{fig:bode_tfest}). The steady state gain was measured to 0.9 for the Simulink model.
\begin{figure}[h]
    \centering
    
    \caption{Bode plot of model's transfer function; voltage to angular velocity}
    \label{fig:bode_tfest}
\end{figure}
The system approximated with Tfest is a 2nd order continuous system, with a fit of 99.4\%. The transfer function for this system is: 
\begin{equation}
    M(s) = \frac{1.77}{s^2+3.82*s+1.96}   
\end{equation}
The poles for this transfer function are $p_1 = -0.61$ and $p_2 = -3.21$. \\
Similarly, by measuring the time constants "by hand" for the drone's angular velocity, $\omega$ and the motors' RPM in the model, the poles become: $p_{\tau \omega} = -0.535$ and $p_{\tau RPM} = -6.87$.  \\
By comparing these two sets of poles, with the transfer function derived in section \ref{sec:airminimal}, it's seen that the modelled system is indeed a good approximation of the real drone. Each pole is roughly within a factor of two of its equivalent pole. Furthermore, it supports the theory that the two lowest frequency poles of the system are associated with the inertia of the system and the mechanical pole in the prop motor.

\subsection{Final controller and implementation}
\subsubsection{Feed-forward gain estimation}
The feed-forward branch was determined by inputting different voltages and recording the drone's steady-state angular velocity. The fit and plot of these data can be seen in fig. \ref{fig:kfestimation}.
\begin{figure}[h!]
    \centering
    
    \caption{Linear fit of angular velocity versus input voltage}
    \label{fig:kfestimation}
\end{figure}
The angular velocity versus input voltage can be approximated as a linear relationship. The gain from the reference $\omega$ to the summation node (see also fig. \ref{fig:controlblock}) before the system becomes:
\begin{equation}
    V = -4.16 + 0.50*\omega_{ref}
\end{equation}
The constant offset is because the motor will not turn on below an input PWM of 13\%.\\
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

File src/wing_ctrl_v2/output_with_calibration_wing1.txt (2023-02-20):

Scanning...

I2C device found at address 0x68  !

I2C device found at address 0x77  !

done

MPU9250 9-axis motion sensor...

MPU9250 I AM 71 I should be 71

MPU9250 is online...

x-axis self test: acceleration trim within : 0.6% of factory value

y-axis self test: acceleration trim within : 0.3% of factory value

z-axis self test: acceleration trim within : 3.9% of factory value

x-axis self test: gyration trim within : -2.0% of factory value

y-axis self test: gyration trim within : -1.1% of factory value

z-axis self test: gyration trim within : -0.4% of factory value

 Calibrate gyro and accel

accel biases (mg)

4.94

31.80

5.86

gyro biases (dps)

5.13

-0.65

0.96

MPU9250 initialized for active data mode....

AK8963 I AM 48 I should be 48

AK8963 initialized for active data mode....

Mag Calibration: Wave device in a figure eight until done!

Mag Calibration done!

AK8963 mag biases (mG)

504.94

588.19

-356.06

AK8963 mag scale (mG)

1.22

1.06

0.80

X-Axis sensitivity adjustment value 1.21

Y-Axis sensitivity adjustment value 1.21

Z-Axis sensitivity adjustment value 1.16

MS5637 pressure sensor reset...

PROM dta read:

C0 = 0

C1 = 0

C2 = 0

C3 = 0

C4 = 0

C5 = 0

C6 = 0

Checksum = 0 , should be 0

ax = 0.00 ay = 0.00 az = 0.00 mg

gx = 0.00 gy = 0.00 gz = 0.00 deg/s

mx = 0 my = 0 mz = 0 mG

q0 = 1.00 qx = 0.00 qy = 0.00 qz = 0.00

Gyro temperature is 26.4 degrees C

Digital temperature value = 20.00 C

Digital temperature value = 68.00 F

Digital pressure value = 0.00 mbar

Altitude = 145366.45 feet

Yaw, Pitch, Roll: 13.80, 0.00, 0.00

Grav_x, Grav_y, Grav_z: 0.00, 0.00, 1000.00 mg

Lin_ax, Lin_ay, Lin_az: 0.00, 0.00, -1000.00 mg

rate = 0.03 Hz

ax = 0.00 ay = 0.00 az = 0.00 mg

gx = 0.00 gy = 0.00 gz = 0.00 deg/s

mx = 0 my = 0 mz = 0 mG

q0 = 1.00 qx = 0.00 qy = 0.00 qz = 0.00

Gyro temperature is 26.4 degrees C

Digital temperature value = 20.00 C

Digital temperature value = 68.00 F

Digital pressure value = 0.00 mbar

Altitude = 145366.45 feet

Yaw, Pitch, Roll: 13.80, 0.00, 0.00

Grav_x, Grav_y, Grav_z: 0.00, 0.00, 1000.00 mg

Lin_ax, Lin_ay, Lin_az: 0.00, 0.00, -1000.00 mg

rate = 50838.77 Hz

ax = 0.00 ay = 0.00 az = 0.00 mg

gx = 0.00 gy = 0.00 gz = 0.00 deg/s

mx = 0 my = 0 mz = 0 mG

q0 = 1.00 qx = 0.00 qy = 0.00 qz = 0.00

Gyro temperature is 26.5 degrees C

Digital temperature value = 20.00 C

Digital temperature value = 68.00 F

Digital pressure value = 0.00 mbar

Altitude = 145366.45 feet

Yaw, Pitch, Roll: 13.80, 0.00, 0.00

Grav_x, Grav_y, Grav_z: 0.00, 0.00, 1000.00 mg

Lin_ax, Lin_ay, Lin_az: 0.00, 0.00, -1000.00 mg

rate = 50847.14 Hz

ax = 0.00 ay = 0.00 az = 0.00 mg

gx = 0.00 gy = 0.00 gz = 0.00 deg/s

mx = 0 my = 0 mz = 0 mG

q0 = 1.00 qx = 0.00 qy = 0.00 qz = 0.00

Gyro temperature is 26.4 degrees C

Digital temperature value = 20.00 C

Digital temperature value = 68.00 F

Digital pressure value = 0.00 mbar

Altitude = 145366.45 feet

Yaw, Pitch, Roll: 13.80, 0.00, 0.00

Grav_x, Grav_y, Grav_z: 0.00, 0.00, 1000.00 mg

Lin_ax, Lin_ay, Lin_az: 0.00, 0.00, -1000.00 mg

rate = 50847.55 Hz

ax = 0.00 ay = 0.00 az = 0.00 mg

gx = 0.00 gy = 0.00 gz = 0.00 deg/s

mx = 0 my = 0 mz = 0 mG

q0 = 1.00 qx = 0.00 qy = 0.00 qz = 0.00

Gyro temperature is 26.5 degrees C

Digital temperature value = 20.00 C

Digital temperature value = 68.00 F

Digital pressure value = 0.00 mbar

Altitude = 145366.45 feet

Yaw, Pitch, Roll: 13.80, 0.00, 0.00

Grav_x, Grav_y, Grav_z: 0.00, 0.00, 1000.00 mg

Lin_ax, Lin_ay, Lin_az: 0.00, 0.00, -1000.00 mg

rate = 50841.00 Hz

ax = 0.00 ay = 0.00 az = 0.00 mg

gx = 0.00 gy = 0.00 gz = 0.00 deg/s

mx = 0 my = 0 mz = 0 mG

q0 = 1.00 qx = 0.00 qy = 0.00 qz = 0.00

Gyro temperature is 26.5 degrees C

Digital temperature value = 20.00 C

Digital temperature value = 68.00 F

Digital pressure value = 0.00 mbar

Altitude = 145366.45 feet

Yaw, Pitch, Roll: 13.80, 0.00, 0.00

Grav_x, Grav_y, Grav_z: 0.00, 0.00, 1000.00 mg

Lin_ax, Lin_ay, Lin_az: 0.00, 0.00, -1000.00 mg

rate = 50848.00 Hz

ax = 0.00 ay = 0.00 az = 0.00 mg

gx = 0.00 gy = 0.00 gz = 0.00 deg/s

mx = 0 my = 0 mz = 0 mG

q0 = 1.00 qx = 0.00 qy = 0.00 qz = 0.00

Gyro temperature is 26.5 degrees C

Digital temperature value = 20.00 C

Digital temperature value = 68.00 F

Digital pressure value = 0.00 mbar

Altitude = 145366.45 feet

Yaw, Pitch, Roll: 13.80, 0.00, 0.00

Grav_x, Grav_y, Grav_z: 0.00, 0.00, 1000.00 mg

Lin_ax, Lin_ay, Lin_az: 0.00, 0.00, -1000.00 mg

rate = 50846.31 Hz

ax = 0.00 ay = 0.00 az = 0.00 mg

gx = 0.00 gy = 0.00 gz = 0.00 deg/s

mx = 0 my = 0 mz = 0 mG

q0 = 1.00 qx = 0.00 qy = 0.00 qz = 0.00

Gyro temperature is 26.5 degrees C

Digital temperature value = 20.00 C

Digital temperature value = 68.00 F

Digital pressure value = 0.00 mbar

Altitude = 145366.45 feet

Yaw, Pitch, Roll: 13.80, 0.00, 0.00

Grav_x, Grav_y, Grav_z: 0.00, 0.00, 1000.00 mg

Lin_ax, Lin_ay, Lin_az: 0.00, 0.00, -1000.00 mg

rate = 50839.74 Hz

ax = 0.00 ay = 0.00 az = 0.00 mg

gx = 0.00 gy = 0.00 gz = 0.00 deg/s

mx = 0 my = 0 mz = 0 mG

q0 = 1.00 qx = 0.00 qy = 0.00 qz = 0.00

Gyro temperature is 26.5 degrees C

Digital temperature value = 20.00 C

Digital temperature value = 68.00 F

Digital pressure value = 0.00 mbar

Altitude = 145366.45 feet

Yaw, Pitch, Roll: 13.80, 0.00, 0.00

Grav_x, Grav_y, Grav_z: 0.00, 0.00, 1000.00 mg

Lin_ax, Lin_ay, Lin_az: 0.00, 0.00, -1000.00 mg

rate = 50848.31 Hz

ax = 0.00 ay = 0.00 az = 0.00 mg

gx = 0.00 gy = 0.00 gz = 0.00 deg/s

mx = 0 my = 0 mz = 0 mG

q0 = 1.00 qx = 0.00 qy = 0.00 qz = 0.00

Gyro temperature is 26.5 degrees C

Digital temperature value = 20.00 C

Digital temperature value = 68.00 F

Digital pressure value = 0.00 mbar

Altitude = 145366.45 feet

Yaw, Pitch, Roll: 13.80, 0.00, 0.00

Grav_x, Grav_y, Grav_z: 0.00, 0.00, 1000.00 mg

Lin_ax, Lin_ay, Lin_az: 0.00, 0.00, -1000.00 mg

rate = 50847.33 Hz

ax = 0.00 ay = 0.00 az = 0.00 mg

gx = 0.00 gy = 0.00 gz = 0.00 deg/s

mx = 0 my = 0 mz = 0 mG

q0 = 1.00 qx = 0.00 qy = 0.00 qz = 0.00

Gyro temperature is 26.5 degrees C

Digital temperature value = 20.00 C

Digital temperature value = 68.00 F

Digital pressure value = 0.00 mbar

Altitude = 145366.45 feet

Yaw, Pitch, Roll: 13.80, 0.00, 0.00

Grav_x, Grav_y, Grav_z: 0.00, 0.00, 1000.00 mg

Lin_ax, Lin_ay, Lin_az: 0.00, 0.00, -1000.00 mg

rate = 50837.69 Hz

ax = 0.00 ay = 0.00 az = 0.00 mg

gx = 0.00 gy = 0.00 gz = 0.00 deg/s

mx = 0 my = 0 mz = 0 mG

q0 = 1.00 qx = 0.00 qy = 0.00 qz = 0.00

Gyro temperature is 26.5 degrees C

Digital temperature value = 20.00 C

Digital temperature value = 68.00 F

Digital pressure value = 0.00 mbar

Altitude = 145366.45 feet

Yaw, Pitch, Roll: 13.80, 0.00, 0.00

Grav_x, Grav_y, Grav_z: 0.00, 0.00, 1000.00 mg

Lin_ax, Lin_ay, Lin_az: 0.00, 0.00, -1000.00 mg

rate = 50848.87 Hz

ax = 0.00 ay = 0.00 az = 0.00 mg

gx = 0.00 gy = 0.00 gz = 0.00 deg/s

mx = 0 my = 0 mz = 0 mG

q0 = 1.00 qx = 0.00 qy = 0.00 qz = 0.00

Gyro temperature is 26.5 degrees C

Digital temperature value = 20.00 C

Digital temperature value = 68.00 F

Digital pressure value = 0.00 mbar

Altitude = 145366.45 feet

Yaw, Pitch, Roll: 13.80, 0.00, 0.00

Grav_x, Grav_y, Grav_z: 0.00, 0.00, 1000.00 mg

Lin_ax, Lin_ay, Lin_az: 0.00, 0.00, -1000.00 mg

rate = 50847.48 Hz

ax = 0.00 ay = 0.00 az = 0.00 mg

gx = 0.00 gy = 0.00 gz = 0.00 deg/s

mx = 0 my = 0 mz = 0 mG

q0 = 1.00 qx = 0.00 qy = 0.00 qz = 0.00

Gyro temperature is 26.5 degrees C

Digital temperature value = 20.00 C

Digital temperature value = 68.00 F

Digital pressure value = 0.00 mbar

Altitude = 145366.45 feet

Yaw, Pitch, Roll: 13.80, 0.00, 0.00

Grav_x, Grav_y, Grav_z: 0.00, 0.00, 1000.00 mg

Lin_ax, Lin_ay, Lin_az: 0.00, 0.00, -1000.00 mg

rate = 50835.09 Hz

ax = 0.00 ay = 0.00 az = 0.00 mg

gx = 0.00 gy = 0.00 gz = 0.00 deg/s

mx = 0 my = 0 mz = 0 mG

q0 = 1.00 qx = 0.00 qy = 0.00 qz = 0.00

Gyro temperature is 26.5 degrees C

Digital temperature value = 20.00 C

Digital temperature value = 68.00 F

Digital pressure value = 0.00 mbar

Altitude = 145366.45 feet

Yaw, Pitch, Roll: 13.80, 0.00, 0.00

Grav_x, Grav_y, Grav_z: 0.00, 0.00, 1000.00 mg

Lin_ax, Lin_ay, Lin_az: 0.00, 0.00, -1000.00 mg

rate = 50848.73 Hz

ax = 0.00 ay = 0.00 az = 0.00 mg

gx = 0.00 gy = 0.00 gz = 0.00 deg/s

mx = 0 my = 0 mz = 0 mG

q0 = 1.00 qx = 0.00 qy = 0.00 qz = 0.00

Gyro temperature is 26.5 degrees C

Digital temperature value = 20.00 C

Digital temperature value = 68.00 F

Digital pressure value = 0.00 mbar

Altitude = 145366.45 feet

Yaw, Pitch, Roll: 13.80, 0.00, 0.00

Grav_x, Grav_y, Grav_z: 0.00, 0.00, 1000.00 mg

Lin_ax, Lin_ay, Lin_az: 0.00, 0.00, -1000.00 mg

rate = 50845.83 Hz

ax = 0.00 ay = 0.00 az = 0.00 mg

gx = 0.00 gy = 0.00 gz = 0.00 deg/s

mx = 0 my = 0 mz = 0 mG

q0 = 1.00 qx = 0.00 qy = 0.00 qz = 0.00

Gyro temperature is 26.5 degrees C

Digital temperature value = 20.00 C

Digital temperature value = 68.00 F

Digital pressure value = 0.00 mbar

Altitude = 145366.45 feet

Yaw, Pitch, Roll: 13.80, 0.00, 0.00

Grav_x, Grav_y, Grav_z: 0.00, 0.00, 1000.00 mg

Lin_ax, Lin_ay, Lin_az: 0.00, 0.00, -1000.00 mg

rate = 50837.40 Hz

ax = 0.00 ay = 0.00 az = 0.00 mg

gx = 0.00 gy = 0.00 gz = 0.00 deg/s

mx = 0 my = 0 mz = 0 mG

q0 = 1.00 qx = 0.00 qy = 0.00 qz = 0.00

Gyro temperature is 26.5 degrees C

Digital temperature value = 20.00 C

Digital temperature value = 68.00 F

Digital pressure value = 0.00 mbar

Altitude = 145366.45 feet

Yaw, Pitch, Roll: 13.80, 0.00, 0.00

Grav_x, Grav_y, Grav_z: 0.00, 0.00, 1000.00 mg

Lin_ax, Lin_ay, Lin_az: 0.00, 0.00, -1000.00 mg

rate = 50848.90 Hz

ax = 0.00 ay = 0.00 az = 0.00 mg

gx = 0.00 gy = 0.00 gz = 0.00 deg/s

mx = 0 my = 0 mz = 0 mG

q0 = 1.00 qx = 0.00 qy = 0.00 qz = 0.00

Gyro temperature is 26.5 degrees C

Digital temperature value = 20.00 C

Digital temperature value = 68.00 F

Digital pressure value = 0.00 mbar

Altitude = 145366.45 feet

Yaw, Pitch, Roll: 13.80, 0.00, 0.00

Grav_x, Grav_y, Grav_z: 0.00, 0.00, 1000.00 mg

Lin_ax, Lin_ay, Lin_az: 0.00, 0.00, -1000.00 mg

rate = 50845.90 Hz

ax = 0.00 ay = 0.00 az = 0.00 mg

gx = 0.00 gy = 0.00 gz = 0.00 deg/s

mx = 0 my = 0 mz = 0 mG

q0 = 1.00 qx = 0.00 qy = 0.00 qz = 0.00

Gyro temperature is 26.5 degrees C

Digital temperature value = 20.00 C

Digital temperature value = 68.00 F

Digital pressure value = 0.00 mbar

Altitude = 145366.45 feet

Yaw, Pitch, Roll: 13.80, 0.00, 0.00

Grav_x, Grav_y, Grav_z: 0.00, 0.00, 1000.00 mg

Lin_ax, Lin_ay, Lin_az: 0.00, 0.00, -1000.00 mg

rate = 50837.29 Hz

ax = 0.00 ay = 0.00 az = 0.00 mg

gx = 0.00 gy = 0.00 gz = 0.00 deg/s

mx = 0 my = 0 mz = 0 mG

q0 = 1.00 qx = 0.00 qy = 0.00 qz = 0.00

Gyro temperature is 26.6 degrees C

Digital temperature value = 20.00 C

Digital temperature value = 68.00 F

Digital pressure value = 0.00 mbar

Altitude = 145366.45 feet

Yaw, Pitch, Roll: 13.80, 0.00, 0.00

Grav_x, Grav_y, Grav_z: 0.00, 0.00, 1000.00 mg

Lin_ax, Lin_ay, Lin_az: 0.00, 0.00, -1000.00 mg

rate = 50849.38 Hz

ax = 0.00 ay = 0.00 az = 0.00 mg

gx = 0.00 gy = 0.00 gz = 0.00 deg/s

mx = 0 my = 0 mz = 0 mG

q0 = 1.00 qx = 0.00 qy = 0.00 qz = 0.00

Gyro temperature is 26.6 degrees C

Digital temperature value = 20.00 C

Digital temperature value = 68.00 F

Digital pressure value = 0.00 mbar

Altitude = 145366.45 feet

Yaw, Pitch, Roll: 13.80, 0.00, 0.00

Grav_x, Grav_y, Grav_z: 0.00, 0.00, 1000.00 mg

Lin_ax, Lin_ay, Lin_az: 0.00, 0.00, -1000.00 mg

rate = 50845.27 Hz

ax = 0.00 ay = 0.00 az = 0.00 mg

gx = 0.00 gy = 0.00 gz = 0.00 deg/s

mx = 0 my = 0 mz = 0 mG

q0 = 1.00 qx = 0.00 qy = 0.00 qz = 0.00

Gyro temperature is 26.6 degrees C

Digital temperature value = 20.00 C

Digital temperature value = 68.00 F

Digital pressure value = 0.00 mbar

Altitude = 145366.45 feet

Yaw, Pitch, Roll: 13.80, 0.00, 0.00

Grav_x, Grav_y, Grav_z: 0.00, 0.00, 1000.00 mg

Lin_ax, Lin_ay, Lin_az: 0.00, 0.00, -1000.00 mg

rate = 50837.52 Hz

ax = 0.00 ay = 0.00 az = 0.00 mg

gx = 0.00 gy = 0.00 gz = 0.00 deg/s

mx = 0 my = 0 mz = 0 mG

q0 = 1.00 qx = 0.00 qy = 0.00 qz = 0.00

Gyro temperature is 26.6 degrees C

Digital temperature value = 20.00 C

Digital temperature value = 68.00 F

Digital pressure value = 0.00 mbar

Altitude = 145366.45 feet

Yaw, Pitch, Roll: 13.80, 0.00, 0.00

Grav_x, Grav_y, Grav_z: 0.00, 0.00, 1000.00 mg

Lin_ax, Lin_ay, Lin_az: 0.00, 0.00, -1000.00 mg

rate = 50849.56 Hz

ax = 0.00 ay = 0.00 az = 0.00 mg

gx = 0.00 gy = 0.00 gz = 0.00 deg/s

mx = 0 my = 0 mz = 0 mG

q0 = 1.00 qx = 0.00 qy = 0.00 qz = 0.00

Gyro temperature is 26.6 degrees C

Digital temperature value = 20.00 C

Digital temperature value = 68.00 F

Digital pressure value = 0.00 mbar

Altitude = 145366.45 feet

Yaw, Pitch, Roll: 13.80, 0.00, 0.00

Grav_x, Grav_y, Grav_z: 0.00, 0.00, 1000.00 mg

Lin_ax, Lin_ay, Lin_az: 0.00, 0.00, -1000.00 mg

rate = 50845.15 Hz

ax = 0.00 ay = 0.00 az = 0.00 mg

gx = 0.00 gy = 0.00 gz = 0.00 deg/s

mx = 0 my = 0 mz = 0 mG

q0 = 1.00 qx = 0.00 qy = 0.00 qz = 0.00

Gyro temperature is 26.6 degrees C

Digital temperature value = 20.00 C

Digital temperature value = 68.00 F

Digital pressure value = 0.00 mbar

Altitude = 145366.45 feet

Yaw, Pitch, Roll: 13.80, 0.00, 0.00

Grav_x, Grav_y, Grav_z: 0.00, 0.00, 1000.00 mg

Lin_ax, Lin_ay, Lin_az: 0.00, 0.00, -1000.00 mg

rate = 50840.16 Hz

ax = 0.00 ay = 0.00 az = 0.00 mg

gx = 0.00 gy = 0.00 gz = 0.00 deg/s

mx = 0 my = 0 mz = 0 mG

q0 = 1.00 qx = 0.00 qy = 0.00 qz = 0.00

Gyro temperature is 26.6 degrees C

Digital temperature value = 20.00 C

Digital temperature value = 68.00 F

Digital pressure value = 0.00 mbar

Altitude = 145366.45 feet

Yaw, Pitch, Roll: 13.80, 0.00, 0.00

Grav_x, Grav_y, Grav_z: 0.00, 0.00, 1000.00 mg

Lin_ax, Lin_ay, Lin_az: 0.00, 0.00, -1000.00 mg

rate = 50848.77 Hz

ax = 0.00 ay = 0.00 az = 0.00 mg

gx = 0.00 gy = 0.00 gz = 0.00 deg/s

mx = 0 my = 0 mz = 0 mG

q0 = 1.00 qx = 0.00 qy = 0.00 qz = 0.00

Gyro temperature is 26.6 degrees C

Digital temperature value = 20.00 C

Digital temperature value = 68.00 F

Digital pressure value = 0.00 mbar

Altitude = 145366.45 feet

Yaw, Pitch, Roll: 13.80, 0.00, 0.00

Grav_x, Grav_y, Grav_z: 0.00, 0.00, 1000.00 mg

Lin_ax, Lin_ay, Lin_az: 0.00, 0.00, -1000.00 mg

rate = 50844.96 Hz

ax = 0.00 ay = 0.00 az = 0.00 mg

gx = 0.00 gy = 0.00 gz = 0.00 deg/s

mx = 0 my = 0 mz = 0 mG

q0 = 1.00 qx = 0.00 qy = 0.00 qz = 0.00

Gyro temperature is 26.6 degrees C

Digital temperature value = 20.00 C

Digital temperature value = 68.00 F

Digital pressure value = 0.00 mbar

Altitude = 145366.45 feet

Yaw, Pitch, Roll: 13.80, 0.00, 0.00

Grav_x, Grav_y, Grav_z: 0.00, 0.00, 1000.00 mg

Lin_ax, Lin_ay, Lin_az: 0.00, 0.00, -1000.00 mg

rate = 50839.42 Hz

ax = 0.00 ay = 0.00 az = 0.00 mg

gx = 0.00 gy = 0.00 gz = 0.00 deg/s

mx = 0 my = 0 mz = 0 mG

q0 = 1.00 qx = 0.00 qy = 0.00 qz = 0.00

Gyro temperature is 26.6 degrees C

Digital temperature value = 20.00 C

Digital temperature value = 68.00 F

Digital pressure value = 0.00 mbar

Altitude = 145366.45 feet

Yaw, Pitch, Roll: 13.80, 0.00, 0.00

Grav_x, Grav_y, Grav_z: 0.00, 0.00, 1000.00 mg

Lin_ax, Lin_ay, Lin_az: 0.00, 0.00, -1000.00 mg

rate = 50848.77 Hz

ax = 0.00 ay = 0.00 az = 0.00 mg

gx = 0.00 gy = 0.00 gz = 0.00 deg/s

mx = 0 my = 0 mz = 0 mG

q0 = 1.00 qx = 0.00 qy = 0.00 qz = 0.00

Gyro temperature is 26.6 degrees C

Digital temperature value = 20.00 C

Digital temperature value = 68.00 F

Digital pressure value = 0.00 mbar

Altitude = 145366.45 feet

Yaw, Pitch, Roll: 13.80, 0.00, 0.00

Grav_x, Grav_y, Grav_z: 0.00, 0.00, 1000.00 mg

Lin_ax, Lin_ay, Lin_az: 0.00, 0.00, -1000.00 mg

rate = 50842.12 Hz

ax = 0.00 ay = 0.00 az = 0.00 mg

gx = 0.00 gy = 0.00 gz = 0.00 deg/s

mx = 0 my = 0 mz = 0 mG

q0 = 1.00 qx = 0.00 qy = 0.00 qz = 0.00

Gyro temperature is 26.6 degrees C

Digital temperature value = 20.00 C

Digital temperature value = 68.00 F

Digital pressure value = 0.00 mbar

Altitude = 145366.45 feet

Yaw, Pitch, Roll: 13.80, 0.00, 0.00

Grav_x, Grav_y, Grav_z: 0.00, 0.00, 1000.00 mg

Lin_ax, Lin_ay, Lin_az: 0.00, 0.00, -1000.00 mg

rate = 50842.04 Hz

ax = 0.00 ay = 0.00 az = 0.00 mg

gx = 0.00 gy = 0.00 gz = 0.00 deg/s

mx = 0 my = 0 mz = 0 mG

q0 = 1.00 qx = 0.00 qy = 0.00 qz = 0.00

Gyro temperature is 26.6 degrees C

Digital temperature value = 20.00 C

Digital temperature value = 68.00 F

Digital pressure value = 0.00 mbar

Altitude = 145366.45 feet

Yaw, Pitch, Roll: 13.80, 0.00, 0.00

Grav_x, Grav_y, Grav_z: 0.00, 0.00, 1000.00 mg

Lin_ax, Lin_ay, Lin_az: 0.00, 0.00, -1000.00 mg

rate = 50848.50 Hz

ax = 0.00 ay = 0.00 az = 0.00 mg

gx = 0.00 gy = 0.00 gz = 0.00 deg/s

mx = 0 my = 0 mz = 0 mG

q0 = 1.00 qx = 0.00 qy = 0.00 qz = 0.00

Gyro temperature is 26.6 degrees C

Digital temperature value = 20.00 C

Digital temperature value = 68.00 F

Digital pressure value = 0.00 mbar

Altitude = 145366.45 feet

Yaw, Pitch, Roll: 13.80, 0.00, 0.00

Grav_x, Grav_y, Grav_z: 0.00, 0.00, 1000.00 mg

Lin_ax, Lin_ay, Lin_az: 0.00, 0.00, -1000.00 mg

rate = 50843.41 Hz

ax = 0.00 ay = 0.00 az = 0.00 mg

gx = 0.00 gy = 0.00 gz = 0.00 deg/s

mx = 0 my = 0 mz = 0 mG

q0 = 1.00 qx = 0.00 qy = 0.00 qz = 0.00

Gyro temperature is 26.6 degrees C

Digital temperature value = 20.00 C

Digital temperature value = 68.00 F

Digital pressure value = 0.00 mbar

Altitude = 145366.45 feet

Yaw, Pitch, Roll: 13.80, 0.00, 0.00

Grav_x, Grav_y, Grav_z: 0.00, 0.00, 1000.00 mg

Lin_ax, Lin_ay, Lin_az: 0.00, 0.00, -1000.00 mg

rate = 50844.27 Hz

ax = 0.00 ay = 0.00 az = 0.00 mg

gx = 0.00 gy = 0.00 gz = 0.00 deg/s

mx = 0 my = 0 mz = 0 mG

q0 = 1.00 qx = 0.00 qy = 0.00 qz = 0.00

Gyro temperature is 26.6 degrees C

Digital temperature value = 20.00 C

Digital temperature value = 68.00 F

Digital pressure value = 0.00 mbar
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

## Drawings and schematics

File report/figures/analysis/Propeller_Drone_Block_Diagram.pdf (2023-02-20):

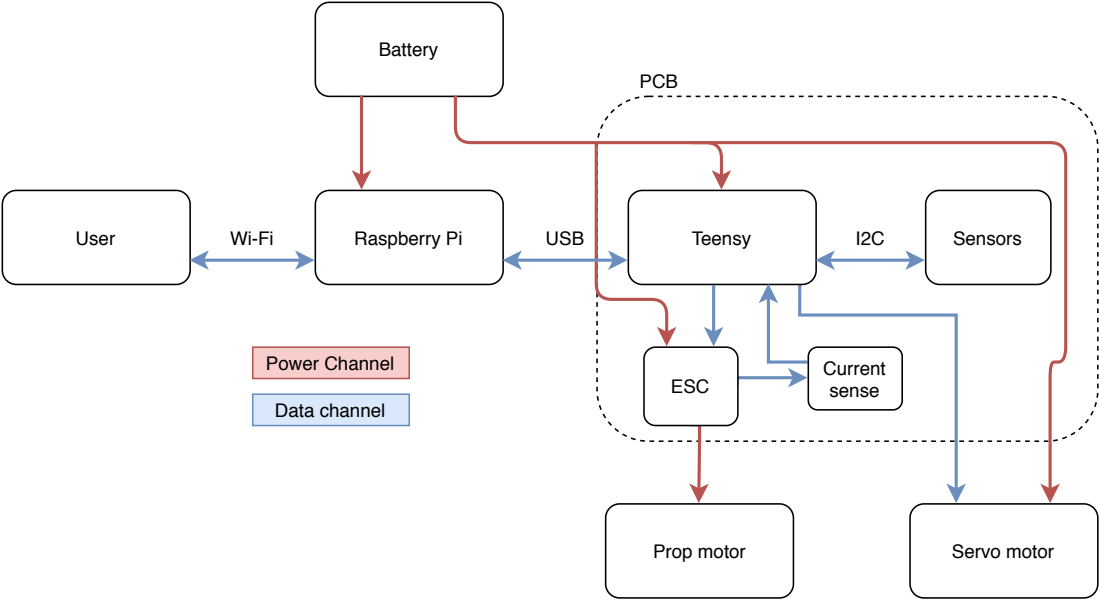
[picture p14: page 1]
Raspberry Pi; Teensy; Sensors; Prop motor; Servo motor; Battery; PCB; User; ESC; Current sense; USB; Power Channel; Data channel

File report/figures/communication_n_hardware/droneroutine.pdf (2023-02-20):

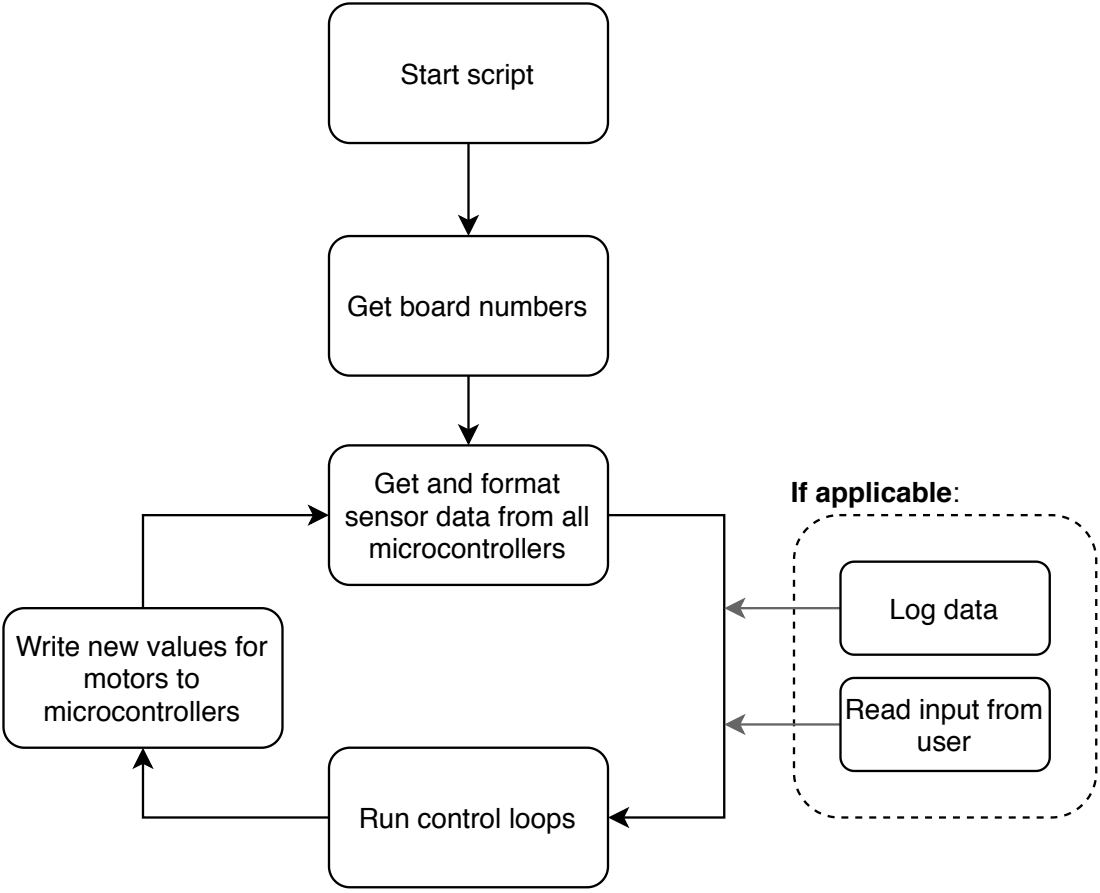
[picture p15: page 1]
Start script; Log data; If applicable:

Get board numbers

Get and format
sensor data from all
microcontrollers

Write new values for
motors to

Read input from
user

Run control loops

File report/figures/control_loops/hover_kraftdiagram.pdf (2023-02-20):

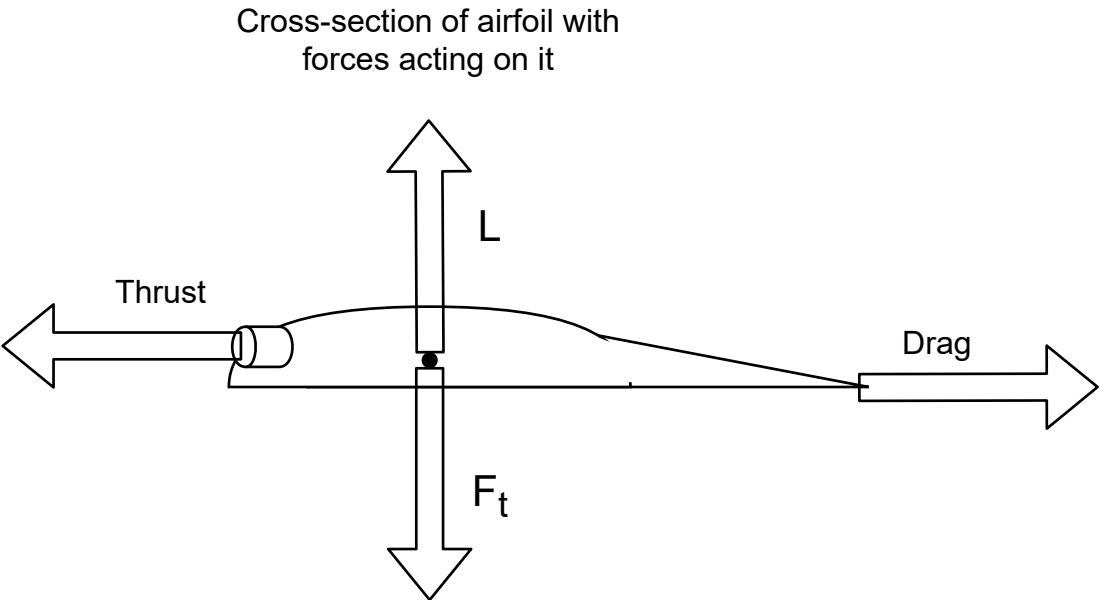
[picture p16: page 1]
Thrust; Drag

Cross-section of airfoil with
forces acting on it

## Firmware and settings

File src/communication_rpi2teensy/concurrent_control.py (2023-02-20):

'''
This code has been developed by Jonas Brøndum (s173952@student.dtu.dk)
and Andreas Grønbech Petersen (s173901@student.dtu.dk) as
part of a Bachelor Thesis in Electrical Engineering at DTU, June 2020
 '''
import threading
import communication_functions as cf
import time
import datetime

# For storing board numbers
board_numbers = [0, 0, 0]

# For storing values for motor control
pwm_vals =[0, 0, 0]  # turns on at about 13
wing_tilt_vals = [90, 90, 90]

# For storing data from sensors
data_string = [0, 0, 0]
current = [0, 0, 0]
voltage = [0, 0, 0]
lin_ax = [0, 0, 0]
lin_ay = [0, 0, 0]
lin_az = [0, 0, 0]
gx = [0, 0, 0]
gy = [0, 0, 0]
gz = [0, 0, 0]
roll = [0, 0, 0]
pitch = [0, 0, 0]
yaw = [0, 0, 0]
time_stamps = [0, 0, 0]

# For checking if there is new data, controlling menu and logging data
choice = ""
newchoice = False
newdata = False
filename_log = ""


# Variables for PD controller
previous_error = 0
set_point = 18 # rad/s
Kp = 1.3
Kd = 0.9
last_time = time.time()
# Feedforward was found using a linear approximation:
# func that defines voltage and rotation ratio: y=2.018*x+8.404
# x=(y-8.404)/2.018 = 0.4955401388*y - 4.164519326
feedforward = 0.4955401388
ff_offset = 4.164519326
fs = 10
sample_time = 1/fs
exitchar = False
last_input = 0

# Control loop, angular velocity, PD controller
def control_angular_velocity(now, dt):
    # Declare global for variables that need changing
    global previous_error, last_time, last_input#, integral

    # Get measured_value as average from the 3 arms
    #measured_value = sum(gz)/len(gz) # if all 3 IMUs work, use this.
    measured_value = sum(gz[1:])/len(gz[1:]) # using avg from arm 2 and 3 due to
                                             # arm1 imu dying on the last day of testing

    # Calculate components
    error = set_point - measured_value
    #integral = integral + error * dt
    derivative = (error - previous_error) / dt
    print("dt:",dt)
    print("derivative:",derivative)

    # Update values for next loop
    previous_error = error
    last_time = now
    last_input = measured_value

    # Combine to get output and return
    # This is a voltage, that needs to be transferred to a PWM signal
    return Kp*error + Kd*derivative + (feedforward * set_point - ff_offset)

# Control_loop is used for running control sequences on the drone.
# At the moment, only control of angular velocity has been implemented
def control_loop():
    # Spawn thread for checking for chars in buffer to exit
    command_thread = threading.Thread(target=getCommand)
    # Set as daemon to kill it when program ends.
    command_thread.daemon = True
    # Start thread
    command_thread.start()

    while True:
        # Check for break command:
        if exitchar is True:
            break
        if command_thread.isAlive() is False:
            command_thread = threading.Thread(target=getCommand)
            command_thread.daemon = True
            command_thread.start()

        # Get time
        now = time.time()
        dt = now-last_time

        # run control loops if sample time is reached
        if sample_time <= dt:
            # Get data from sensors
            threads_read_sensor_data()

            # Log it
            log_sensor_data()

            # Get the voltage for the motors
            voltage = control_angular_velocity(now, dt)

            # Convert to PWM
            pwm = vol2pwm(voltage)
            pwm_vals[0] = pwm
            pwm_vals[1] = pwm
            pwm_vals[2] = pwm
            # Write it
            threads_write_pwm_propeller()

            # For debugging
            print("Voltage:",voltage)
            print("Angular vel:",sum(gz[1:])/len(gz[1:]))#sum(gz)/len(gz))
            print("")

# Used for checking input buffer when program is running
# called as seperate thread to not stall program
def getCommand():
    global exitchar, set_point, wing_tilt_vals
    # Get input
    char = input()
    # If it contains anything:
    if len(char) > 0:

        # sp is for changing setpoint of the PD controller while loop is running
        if char[:2] == 'sp':
            tmp = int(char[3:])
            set_point = tmp
        # a is for changing the wing tilt while the loop is running
        elif char[0] == 'a':
            # Extract value
            tmp = int(char[2:])
            # Update arrays
            wing_tilt_vals[0] = tmp
            wing_tilt_vals[1] = tmp
            wing_tilt_vals[2] = tmp
            # Write new angle
            threads_write_wing_tilt()

        # everything else is used as exit chars
        else:
            exitchar = True



# Converts a voltage level to a PWM level
def vol2pwm(vol):
    # Calculate current max in terms of voltage available on the drone
    maxvol = sum(voltage)/len(voltage)
    # If some error happend, set it to standard 11 volts
    if maxvol <= 1:
        maxvol = 11
    # Calculate pwm level
    pwm = int((vol/maxvol) * 100)
    # If unuseable result, set it to something useful
    if pwm>100:
        pwm = 100
    if pwm < 1:
        pwm = 0
    return pwm




# Get board number to correlate Serial object and arm number
# index is integer referring to whcih serUSB object
def get_board_number_wrapper(serUSB, index):
    global board_numbers

    raw = cf.getBoardNumber(serUSB)
    number = raw.decode()

    if len(number) < 1:
        # if len > 0 is false, try again
        get_board_number_wrapper(serUSB, index)
    try:
        number = int(number[0])
        board_numbers[index] = number

    except:
        print("Error in getting boardnumber, trying again")
        get_board_number_wrapper(serUSB, index)



# Get sensor data from 1 Teensy and put it into correct arrays
def get_sensor_data_wrapper(serUSB, i):
    #global sensor_data
    global current, voltage, lin_ax, lin_ay, lin_az, gx, gy, gz, roll, pitch ,yaw

    # getting data and putting it into sensor_data array for temp storage
    raw = cf.getAllSensorData(serUSB)

    # convert from byte to str
    datastr = raw.decode()

    # put it into correct array, used when logging
    data_string[i] = datastr

    # put data into correct arrays with float format
    # Format I U lin_ax lin_ay lin_az gx gy gz roll pitch yaw
    if len(datastr) > 0:
        data = datastr.split(" ")
        if len(data) > 10:
            time_stamps[i] = time.time() - start_time
            current[i] = float(data[0])
            voltage[i] = float(data[1])
            lin_ax[i] = float(data[2])
            lin_ay[i] = float(data[3])
            lin_az[i] = float(data[4])
            gx[i] = float(data[5])
            gy[i] = float(data[6])
            gz[i] = float(data[7])
            roll[i] = float(data[8])
            pitch[i] = float(data[9])
            yaw[i] = float(data[10])
        else:
            print("Error: Length of read data was not > 10")
            return -1

    else:
        print("Error: Length of read data was not > 0")

# Writes pwm value from pwm_vals to Teensy
def write_pwm_propeller_wrapper(serUSB, index):
    cf.set_prop_motor_PWM(serUSB, pwm_vals[index])

# Writes angle from wing_tilt_vals to Teensy
def write_wing_tilt_wrapper(serUSB, index):
    cf.set_wing_tilt(serUSB, wing_tilt_vals[index])

# Put data from all 3 arms into 1 string and write it to logfile
def log_sensor_data():
    # Make newdata global to edit status
    global newdata

    # If there is new data ready, treat it
    if newdata is True:
        # Create 1 long string with timestamps and data, modifying array length is to remove EOL chars
        record = (str(time_stamps[0]) + " " + data_string[0][:len(data_string[0])-1] +";" +
        str(time_stamps[1]) + " " + data_string[1][:len(data_string[1])-1] + ";" +
        str(time_stamps[2]) + " " + data_string[2][:len(data_string[2])-1] + ";" + str(pwm_vals[0]) + ";" + str(wing_tilt_vals[0]) + ";" + str(set_point) + "\n")

        # Write it to the logfile
        with open(filename_log, 'a') as f:
            f.write(record)

        # Set newdata flag to False
        newdata = False

# Spawning 3 threads for getting data from each Teensy
def threads_read_sensor_data():
    # Spawn threads
    sensor1 = threading.Thread(target=get_sensor_data_wrapper, args=(cf.serUSB1, board_numbers[0]-1))
    sensor2 = threading.Thread(target=get_sensor_data_wrapper, args=(cf.serUSB2, board_numbers[1]-1))
    sensor3 = threading.Thread(target=get_sensor_data_wrapper, args=(cf.serUSB3, board_numbers[2]-1))

    # Start threads
    sensor1.start()
    sensor2.start()
    sensor3.start()

    # Force them to wait for all each other to finish
    sensor1.join()
    sensor2.join()
    sensor3.join()

    # Set newdata flag to True, because there is new data ready
    global newdata
    newdata = True


# Spawning 3 threads for writing pwm to each Teensy
def threads_write_pwm_propeller():
    # Spawn threads
    # index for correct value is found by getting board number and subtracting 1 because board numbers are 1 indexed
    pwm1 = threading.Thread(target=write_pwm_propeller_wrapper, args=(cf.serUSB1, board_numbers[0]-1))
    pwm2 = threading.Thread(target=write_pwm_propeller_wrapper, args=(cf.serUSB2, board_numbers[1]-1))
    pwm3 = threading.Thread(target=write_pwm_propeller_wrapper, args=(cf.serUSB3, board_numbers[2]-1))

    # Start threads
    pwm1.start()
    pwm2.start()
    pwm3.start()

    # Force them to wait for each other to finish
    pwm1.join()
    pwm2.join()
    pwm3.join()


# Spawning 3 threads for writing angle to each Teensy
def threads_write_wing_tilt():
    # Spawn threads
    pwm1 = threading.Thread(target=write_wing_tilt_wrapper, args=(cf.serUSB1, board_numbers[0]-1))
    pwm2 = threading.Thread(target=write_wing_tilt_wrapper, args=(cf.serUSB2, board_numbers[1]-1))
    pwm3 = threading.Thread(target=write_wing_tilt_wrapper, args=(cf.serUSB3, board_numbers[2]-1))

    # Start threads
    pwm1.start()
    pwm2.start()
    pwm3.start()

    # Force them to wait for each other
    pwm1.join()
    pwm2.join()
    pwm3.join()


# Spawning 3 threads for getting data from each Teensy
def threads_get_board_numbers():
    # Spawn threads
    sensor1 = threading.Thread(target=get_board_number_wrapper, args=(cf.serUSB1, 0))
    sensor2 = threading.Thread(target=get_board_number_wrapper, args=(cf.serUSB2, 1))
    sensor3 = threading.Thread(target=get_board_number_wrapper, args=(cf.serUSB3, 2))

    # Start threads
    sensor1.start()
    sensor2.start()
    sensor3.start()

    # Force them to wait for all each other to finish
    sensor1.join()
    sensor2.join()
    sensor3.join()


# Write PWM of 0 to each Teensy
def kill_motors():
    print("Turning off propeller motors")
    cf.set_prop_motor_PWM(cf.serUSB1, 0)
    cf.set_prop_motor_PWM(cf.serUSB2, 0)
    cf.set_prop_motor_PWM(cf.serUSB3, 0)


# Read input from terminal. Useful when used as a thread daemon
def read_choice():
    global choice, newchoice

    # Start loop for infinite tries
    while True:
        # Get input from user
        choice = input()
        try:
            # Check if first char is an int
            tmp = int(choice[0])
        except:
            # Not an int, react:
            print("Valid number, please")
            continue
        # Check range of input
        if 0 <= tmp <= 5:
            # Range of input OK, update newchoice flag to tell menuloop
            # that it has to react on new stuff
            newchoice = True
            break
        else:
            # React on invalid range
            print("Valid range, please")


# Print help menu
def helpmenu():
    print("0: For this menu")
    print("1: Get data_string")
    print("2: Write PWM, 0-100")
    print("3: Write tilt, 0-180")
    print("4: Print board number and SerUSB name")
    print("5: Quit")


# Menu for debugging, infinite loop with different commands
def menu():
    # Set newchoice global for editing
    global newchoice, pwm_vals, wing_tilt_vals

    # Print info
    print("Debugging menu.")
    print("Format is: int=val, ie. 2=20 for sending pwm of 20 ")
    helpmenu() # print rest of menu


    # Spawn thread for reading input from user
    input_thread = threading.Thread(target=read_choice)
    # Set as daemon to kill it when program ends.
    input_thread.daemon = True
    # Start thread
    input_thread.start()



    # Run infinite loop
    while True:
        # Check for new input from user
        if newchoice is False:
            # If there is no thread for reading from user, spawn 1
            if input_thread.is_alive() is False:
                input_thread = threading.Thread(target=read_choice)
                input_thread.daemon = True
                input_thread.start()
        # React on new input from user
        if newchoice is True:
            newchoice = False  # set flag to false
            command = int(choice[0]) # 1 int is the menu choice

            # See help menu
            if command == 0:
                helpmenu()

            # Print data string to terminal
            elif command == 1:
                print(data_string)

            # Write PWM to motor
            elif command == 2:
                # Convert to int from string
                tmp = int(choice[2:])
                print("Writing new pwm values")

                # Update global PWM array
                pwm_vals[0] = tmp
                pwm_vals[1] = tmp
                pwm_vals[2] = tmp

                # Write to all motors
                threads_write_pwm_propeller()

            # Write new angle
            elif command == 3:
                # Conver to int from string
                tmp = int(choice[2:])
                print("Writing new tilt values")

                # Update global tilt array
                wing_tilt_vals[0] = tmp
                wing_tilt_vals[1] = tmp
                wing_tilt_vals[2] = tmp

                # Write to all motors
                threads_write_wing_tilt()
            elif command == 4:
                print("SerUSB1 =", board_numbers[0])
                print("SerUSB2 =", board_numbers[1])
                print("SerUSB3 =", board_numbers[2])
                # Exit
            elif command == 5:
                    break
        #update_frequency = 75 # Hz
        #time.sleep(1/update_frequency)

        # Makes sure there aren't too many threads. Usually about 2 in total, but
        # had issue with program dying at 250 threads
        # Probably not nescessary any longer, issue has been fixed
        if threading.active_count() < 200:
            threads_read_sensor_data()

        # Run function to log data. Function only logs if new data has arrived,
        # otherwise it just returns
        log_sensor_data()


# Create logfile with todays date and time as name, .txt
def create_logfile():
    global filename_log
    now = datetime.datetime.now()
    now =  now.strftime("%Y-%m-%d_%H-%M-%S")
    filename_log = now + ".txt"


    with open(filename_log, 'a') as f:
        f.write(now + "\n")


def get_wingtilt_on_startup():
    print("Please choose desired tilt angle")
    while True:
        # Get input from user
        start_angle = input("0 to 180: ")
        try:
            # Check if first char is an int
            tmp = int(start_angle[0])
            wing_tilt_vals[0] = int(start_angle)
            wing_tilt_vals[1] = int(start_angle)
            wing_tilt_vals[2] = int(start_angle)
            break;
        except:
            # Not an int, react:
            print("Valid number, please")
            continue

# Starting script
if __name__ == '__main__':
    print("Staring...")

    # get start of time for runtime
    start_time = time.time()

    # Choose wing tilt angle first, to get a correct angle in log
    # in case you were trying to reuse angle from last time
    get_wingtilt_on_startup()

    threads_write_wing_tilt()
    # create logfile with todays date and time as name
    create_logfile()

    # get board board_numbers
    threads_get_board_numbers()

    ## main menu, infinite loop for controlling and debugging
    #menu()

    print("To set a new setpoint, use \"sp=val\"")
    print("To exit: Any char except \"sp\" + enter")
    control_loop()


    # make sure to shut off motors
    kill_motors()

    print("Finished.")
    print("Runtime:  --- %s seconds ---" % (time.time() - start_time))

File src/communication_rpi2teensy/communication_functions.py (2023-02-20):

import serial  # important to install pyserial and not serial, as in "pip3 install pyserial"


read_timeout = 0.01  # timeout when reading from USB, mostly useless due to us using readline()

# Declaration of Serial objects, one for each of the three Teensy boards

serUSB1 = serial.Serial(
    port='/dev/ttyACM0',  # Get correct port using 'dmesg | grep tty' and find active one
    baudrate=115200,  # USB is always 12 Mbit/sec
    parity=serial.PARITY_NONE,
    stopbits=serial.STOPBITS_ONE, # pretty sure stopbits is unused by USB
    bytesize=serial.EIGHTBITS,
    timeout=read_timeout
)
serUSB2 = serial.Serial(
    port='/dev/ttyACM1',  # Get correct port using 'dmesg | grep tty' and find active one
    baudrate=115200,  # USB is always 12 Mbit/sec
    parity=serial.PARITY_NONE,
    stopbits=serial.STOPBITS_ONE, # pretty sure stopbits is unused by USB
    bytesize=serial.EIGHTBITS,
    timeout=read_timeout
)
serUSB3 = serial.Serial(
    port='/dev/ttyACM2',  # Get correct port using 'dmesg | grep tty' and find active one
    baudrate=115200,  # USB is always 12 Mbit/sec
    parity=serial.PARITY_NONE,
    stopbits=serial.STOPBITS_ONE, # pretty sure stopbits is unused by USB
    bytesize=serial.EIGHTBITS,
    timeout=read_timeout
)

# Get board number used in calibration on Teensy to correctly indicate
# which arm is which when logging. Other solution is to turn the Teensys on in
# the desired order. RPi names the usb ports after which thing is correct first
def getBoardNumber(serUSB):
    # Remove stuff in buffer, maybe useless
    serUSB.flush()

    # Create string, encode and send it.
    write_string = 'q=1\r\n'
    serUSB.write(write_string.encode('utf-8'))

    # Loop for reading response
    while True:
        try:
            # Get input, stops reading after EOL char
            readOut = serUSB.readline()
            break

        except:
            print("Could not read.")
            pass
    # Return data
    return readOut


# send A=1 to teensy, which returns all data
# only send \n from Teensy, receving device is RPI, where EOL char is \n
def getAllSensorData(serUSB):
    # Remove stuff in buffer
    serUSB.flush()

    # Create string, encode and send it.
    write_string = 'A=1\r\n'
    serUSB.write(write_string.encode('utf-8'))

    # Loop for reading response
    while True:
        try:
            # Get input, stops reading after EOL char
            readOut = serUSB.readline()
            break
        except:
            print("Could not read.")
            pass
    # Return data
    return readOut


# function for writing PWM val to Teensy, from 0 to 100,
# Starts at about PWM=13, 31/3/2020
def set_prop_motor_PWM(serUSB, PWM):
    # Clear buffer
    serUSB.flush()

    # Create string
    PWM_string = 'D=' + str(PWM) + '\n'  # format needed by Teensy

    # Send it
    serUSB.write(PWM_string.encode('utf-8'))


# write wing tilt angle to Teensy
# 90 is horizontal
def set_wing_tilt(serUSB, angle):
    # Clear buffer
    serUSB.flush()

    # Create string
    PWM_string = 'c=' + str(angle) + '\n'  # format needed by Teensy

    # Send it
    serUSB.write(PWM_string.encode('utf-8'))
